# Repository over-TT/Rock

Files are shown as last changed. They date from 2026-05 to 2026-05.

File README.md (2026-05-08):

# Rock

Simple 3D printed RC car with a brushless drone motor. Drive it from your phone over WiFi.

<p align="center">
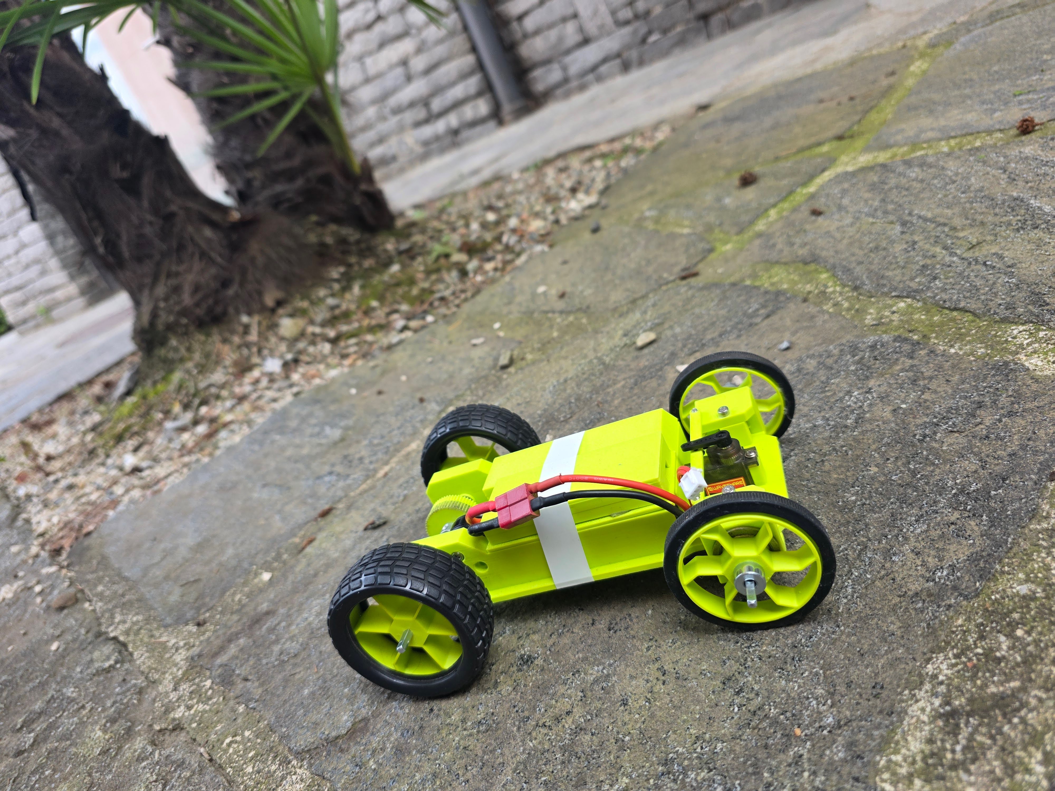
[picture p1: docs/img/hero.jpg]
Rock RC car
  
</p>
---

## Repo

- `firmware/controller/` — controller code
- `firmware/car/` — car code
- `cad/` — 3mf files to print

CAD on MakerWorld: TBD

---

## Parts

**Electronics**
- ReadyToSky MT2204 2300KV brushless drone motor
- EMAX Bullet 20A BLHeli-S ESC
- MG90S servo
- XIAO ESP32-S3 (controller)
- LilyGO T-Energy S3 (car)
- 2S 7.4V 1800mAh LiPo, T-plug ([Reely](https://www.conrad.ch/de/p/reely-modellbau-akkupack-lipo-7-4-v-1800-mah-zellen-zahl-2-racingpack-t-buchse-2901784.html))
- T-plug pigtail
- Wire

**Drivetrain**
- 10T pinion (store bought, fits motor shaft)
- 58T spur gear (printed)
- 1/4" (6.35 mm) square steel drive shaft
- 4x flanged ball bearings (~22 mm OD x ~7.6 mm ID x ~7 mm wide)
- 4x shaft collars for 1/4" square shaft
- Steering linkage

**3D printed parts**
- Body
- 58T spur gear
- 2x front wheels
- 2x rear wheels
- 2x steering knuckles (hold the front wheels, pivot for steering)
- 4x square inserts (adapt the round bearing to the square shaft)
- Battery cover
- ESP cover

**Hardware**
- M3 heat set inserts, screws, nuts
- 4x rubber tires for the printed wheels

---

## Wiring

Car ESP32:

```
ESC signal   -> GPIO 9
Servo signal -> GPIO 10
Servo V+     -> 5V (ESC BEC)
ESP32 5V     -> 5V (ESC BEC)
GND          -> GND
```

GPIO numbers refer to the ESP32 GPIO scheme, not silkscreen pin numbers. If you flash on a different ESP32 variant (XIAO ESP32-S3, ESP32-C3, etc.), check the board's pinout — GPIO 9/10 may map to a different physical pin.

LiPo to ESC via T-plug. Don't run USB and BEC into the ESP32 at the same time.

Controller is the XIAO on USB. No wiring.

---

## Flash

Arduino IDE, `esp32` core 2.0+ from Boards Manager.

Libraries:
- ESP32Servo
- WebSockets (Markus Sattler)

Open `firmware/controller/controller.ino`, pick your board, upload. Same for `firmware/car/car.ino` (LiPo unplugged when uploading).

ESC was set up once with BLHeli Suite using an Arduino Nano running the BLHeli passthrough sketch.

---

## Drive it

1. Power the controller.
2. Phone WiFi → `ROCK_RC`, password `12345678`.
3. Browser → `http://192.168.4.1`
4. Power the car. UI shows "Car: Connected".
5. Left stick throttle, right stick steering. Show Settings for trim, max speed, ramp step.

---

## Tuning

If forward/reverse or left/right is swapped, swap the values in `car.ino`:
- `ESC_FORWARD` / `ESC_REVERSE`
- `SERVO_LEFT` / `SERVO_RIGHT` (90 = center)

Trim, max speed, and ramp step are sliders in the UI.

---

## TODO

- CAD on MakerWorld
- Wiring diagram image
- Demo video
- Battery voltage in UI
- Proper retention for battery / ESC / ESP32 (snap-fit or clamps instead of tape)

---

## License

- Code (`firmware/`): MIT — see [LICENSE](LICENSE)
- CAD (`cad/`): CC BY-SA 4.0 — see [cad/LICENSE](cad/LICENSE)

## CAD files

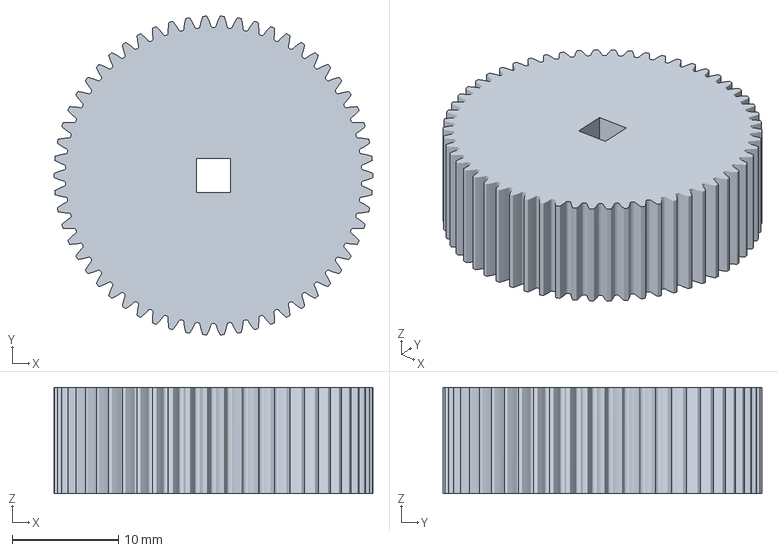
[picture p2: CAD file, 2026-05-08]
cad/spur_58t.3mf
30.0 x 30.0 x 10.0 mm

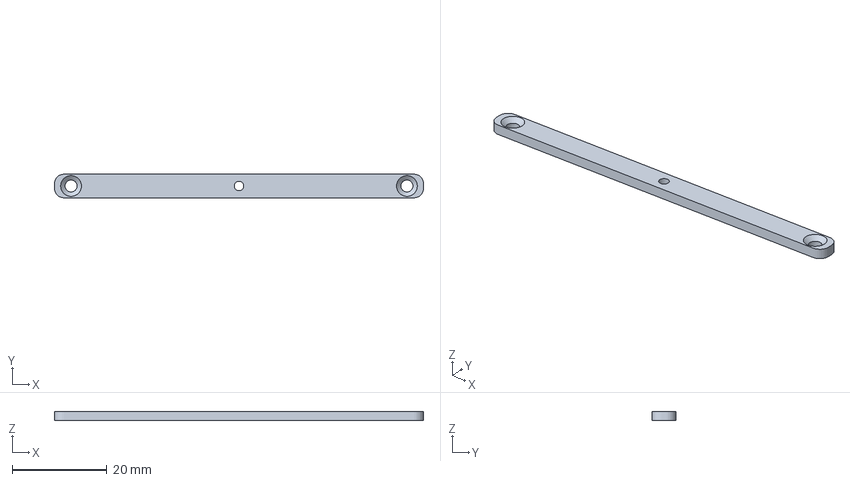
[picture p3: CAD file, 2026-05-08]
cad/steering_link.3mf
78.0 x 5.00 x 2.00 mm

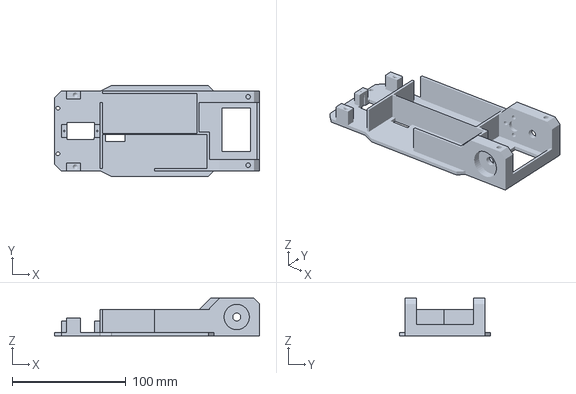
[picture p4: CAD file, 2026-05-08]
cad/chassis.3mf
180.0 x 80.0 x 33.0 mm

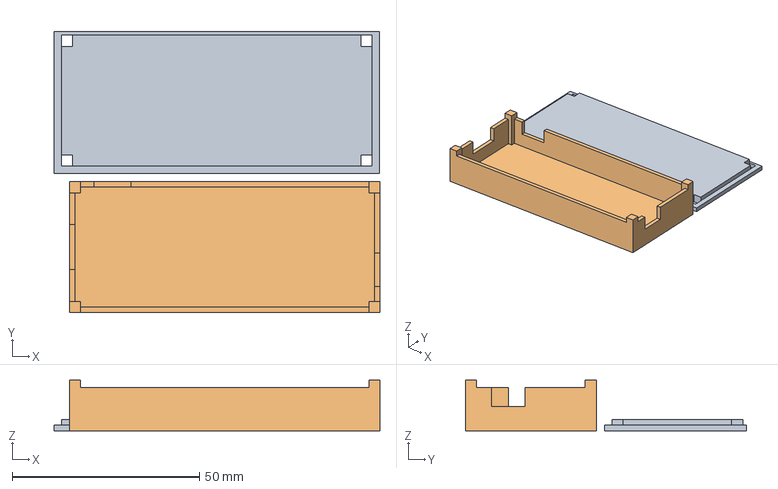
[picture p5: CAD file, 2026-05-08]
cad/battery_cover.3mf
87.1 x 75.1 x 13.5 mm

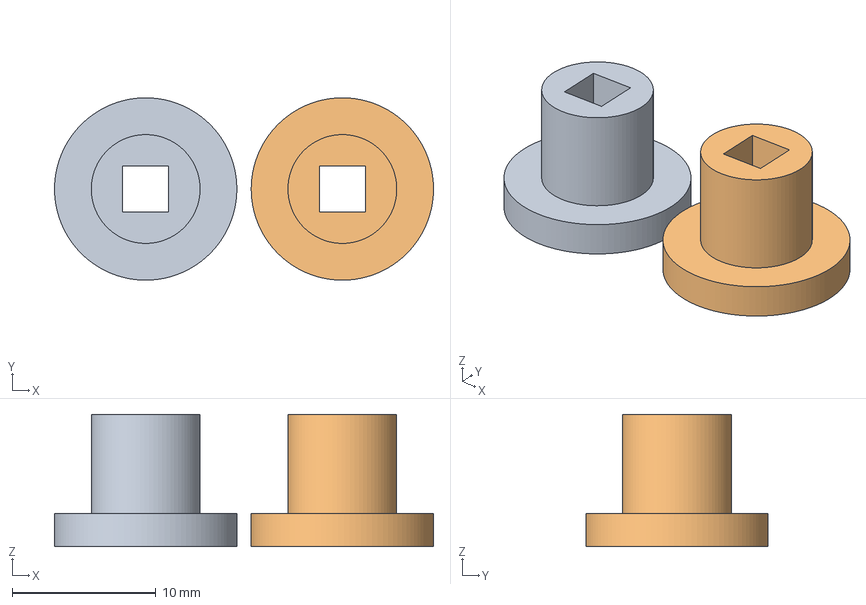
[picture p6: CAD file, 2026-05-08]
cad/bearing_insert.3mf
26.4 x 12.7 x 9.20 mm

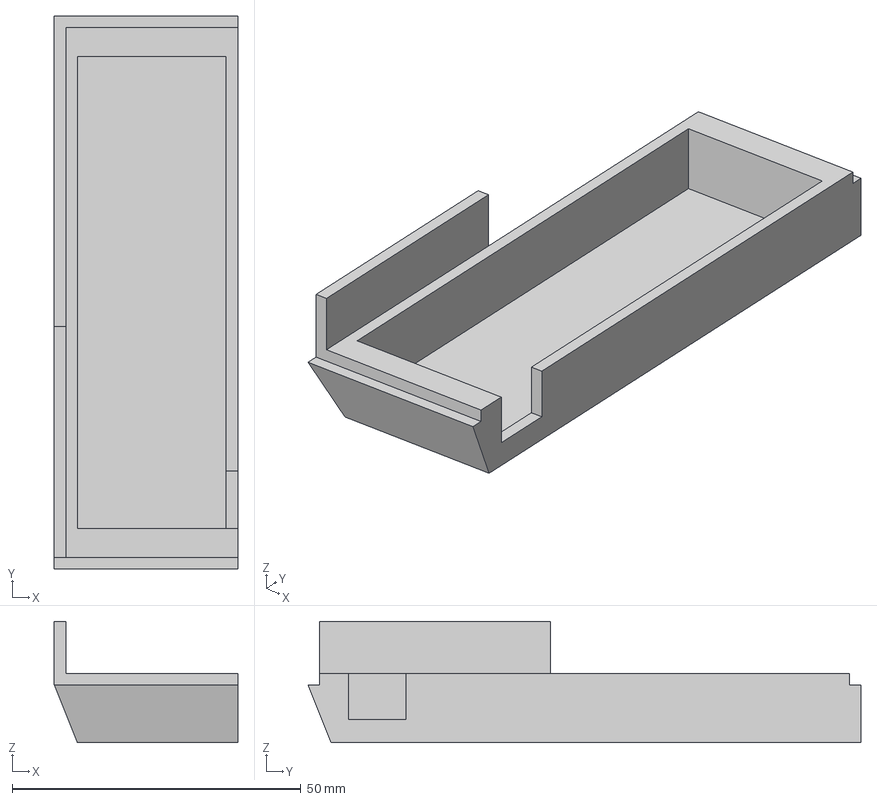
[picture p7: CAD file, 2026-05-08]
cad/electronics_cover.3mf
31.8 x 95.8 x 21.0 mm

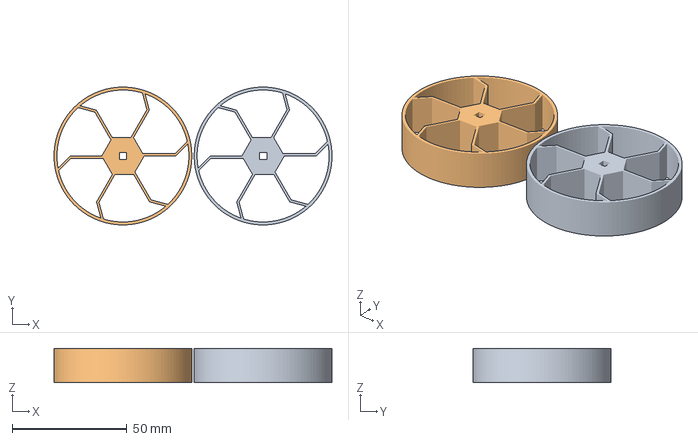
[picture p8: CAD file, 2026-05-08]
cad/rear_wheel.3mf
121.0 x 60.0 x 15.0 mm

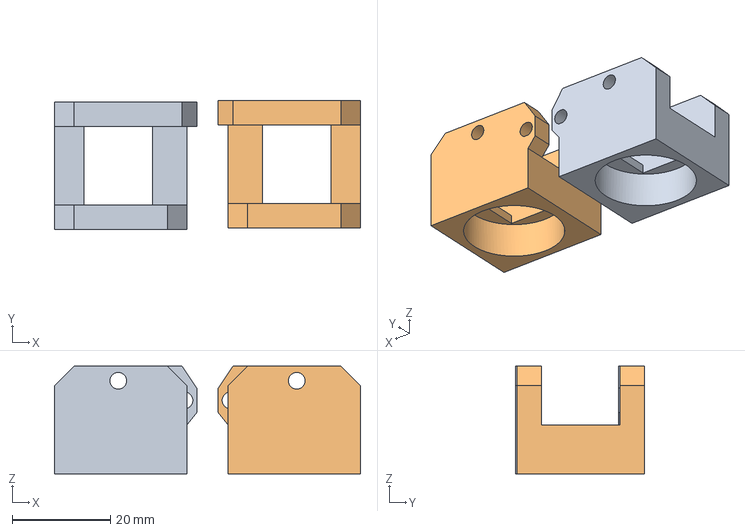
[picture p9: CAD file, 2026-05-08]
cad/steering_knuckle .3mf
62.4 x 26.3 x 22.0 mm

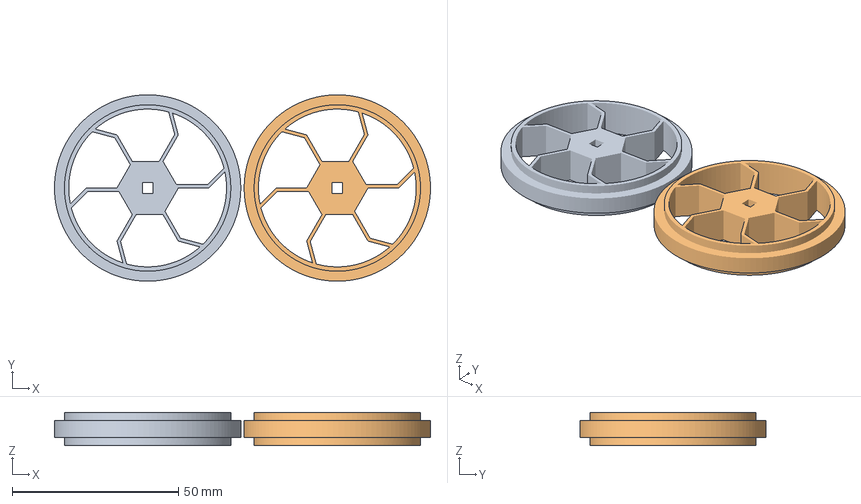
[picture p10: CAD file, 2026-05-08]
cad/front_wheel.3mf
113.0 x 56.0 x 10.0 mm

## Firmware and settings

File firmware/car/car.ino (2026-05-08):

// ROCK RC - Car firmware (ESP32)
// Receives ESP-NOW control packets, drives the ESC and steering servo,
// and reports status back to the controller. Failsafe stops the car if
// packets stop arriving.
// Licensed under the MIT License. See LICENSE at the repository root.

#include <WiFi.h>
#include <esp_now.h>
#include <esp_wifi.h>
#include <esp_arduino_version.h>
#include <ESP32Servo.h>

Servo esc;
Servo steeringServo;

// ===== PINS =====
// These pins are for the board used in this build.
// Change them if using a different ESP32 board.
// Always check the actual GPIO pinout before wiring.
const int ESC_PIN = 9;
const int SERVO_PIN = 10;

// ===== ESP-NOW SETTINGS =====
const int WIFI_CHANNEL = 6;

// ===== ESP-NOW TYPES =====
const uint8_t TYPE_CONTROL = 1;
const uint8_t TYPE_STATUS  = 2;

// ===== ESC SETTINGS =====
const int ESC_MIN_ATTACH = 1000;
const int ESC_MAX_ATTACH = 2000;

const int ESC_FORWARD = 1200;
const int ESC_NEUTRAL = 1500;
const int ESC_REVERSE = 1700;

// If motor direction is backwards, swap ESC_FORWARD and ESC_REVERSE.

// ===== SERVO SETTINGS =====
const int SERVO_MIN_ATTACH = 500;
const int SERVO_MAX_ATTACH = 2500;

const int SERVO_LEFT = 120;
const int SERVO_CENTER = 90;
const int SERVO_RIGHT = 60;

// ===== SAFETY =====
unsigned long lastCommandTime = 0;
const unsigned long FAILSAFE_TIME = 500;

// ===== MOTOR RAMPING =====
const unsigned long RAMP_INTERVAL = 20;
unsigned long lastRampTime = 0;

// ===== STATUS SENDING =====
const unsigned long STATUS_INTERVAL = 200;
unsigned long lastStatusSend = 0;

// Control values
int targetMotor = 0;
int currentMotor = 0;
int targetSteer = 0;

int servoOffset = 0;
int maxSpeed = 60;
int rampStep = 4;

int currentThrottlePulse = ESC_NEUTRAL;
int currentSteeringAngle = SERVO_CENTER;

bool failsafeActive = false;

uint8_t controllerMac[6];
bool controllerKnown = false;
bool controllerPeerAdded = false;
bool needAddControllerPeer = false;

uint32_t lastSeqReceived = 0;

// ===== CONTROL PACKET =====
// Must match controller code EXACTLY
typedef struct __attribute__((packed)) {
  uint8_t type;
  int16_t motor;
  int16_t steer;
  int16_t servoOffset;
  uint8_t maxSpeed;
  uint8_t rampStep;
  uint32_t seq;
} ControlPacket;

// ===== STATUS PACKET =====
// Must match controller code EXACTLY
typedef struct __attribute__((packed)) {
  uint8_t type;
  uint32_t lastSeqReceived;
  int16_t targetMotor;
  int16_t currentMotor;
  int16_t steeringAngle;
  uint8_t maxSpeed;
  uint8_t rampStep;
  uint8_t failsafeActive;
} CarStatusPacket;

ControlPacket incoming;
CarStatusPacket statusPacket;

void printMac(const uint8_t *mac) {
  for (int i = 0; i < 6; i++) {
    if (mac[i] < 16) Serial.print("0");
    Serial.print(mac[i], HEX);
    if (i < 5) Serial.print(":");
  }
}

void addControllerPeerIfNeeded() {
  if (!controllerKnown) return;
  if (!needAddControllerPeer && controllerPeerAdded) return;

  if (esp_now_is_peer_exist(controllerMac)) {
    controllerPeerAdded = true;
    needAddControllerPeer = false;
    return;
  }

  esp_now_peer_info_t peerInfo = {};
  memcpy(peerInfo.peer_addr, controllerMac, 6);
  peerInfo.channel = WIFI_CHANNEL;
  peerInfo.encrypt = false;

  if (esp_now_add_peer(&peerInfo) == ESP_OK) {
    controllerPeerAdded = true;
    needAddControllerPeer = false;

    Serial.print("Controller paired: ");
    printMac(controllerMac);
    Serial.println();
  } else {
    Serial.println("Failed to add controller peer");
  }
}

void sendStatusToController() {
  if (!controllerPeerAdded) return;

  statusPacket.type = TYPE_STATUS;
  statusPacket.lastSeqReceived = lastSeqReceived;
  statusPacket.targetMotor = targetMotor;
  statusPacket.currentMotor = currentMotor;
  statusPacket.steeringAngle = currentSteeringAngle;
  statusPacket.maxSpeed = maxSpeed;
  statusPacket.rampStep = rampStep;
  statusPacket.failsafeActive = failsafeActive ? 1 : 0;

  esp_now_send(controllerMac, (uint8_t*)&statusPacket, sizeof(statusPacket));
}

void applyMotorPulseFromValue(int motorValue) {
  motorValue = constrain(motorValue, -100, 100);

  int pulse;

  if (abs(motorValue) < 5) {
    pulse = ESC_NEUTRAL;
  } else if (motorValue > 0) {
    pulse = map(motorValue, 0, 100, ESC_NEUTRAL, ESC_FORWARD);
  } else {
    pulse = map(motorValue, 0, -100, ESC_NEUTRAL, ESC_REVERSE);
  }

  pulse = constrain(pulse, ESC_MIN_ATTACH, ESC_MAX_ATTACH);

  currentThrottlePulse = pulse;
  esc.writeMicroseconds(currentThrottlePulse);
}

void applySteering(int steerValue) {
  steerValue = constrain(steerValue, -100, 100);

  int angle;

  if (abs(steerValue) < 5) {
    angle = SERVO_CENTER;
  } else {
    angle = map(steerValue, -100, 100, SERVO_LEFT, SERVO_RIGHT);
  }

  angle += servoOffset;
  angle = constrain(angle, 0, 180);

  currentSteeringAngle = angle;
  steeringServo.write(currentSteeringAngle);
}

void updateMotorRamp() {
  if (millis() - lastRampTime < RAMP_INTERVAL) return;
  lastRampTime = millis();

  int difference = targetMotor - currentMotor;

  if (difference == 0) {
    applyMotorPulseFromValue(currentMotor);
    return;
  }

  int step = rampStep;

  // Symmetric ramping:
  // forward, reverse, speeding up, slowing down all use same step.
  if (abs(difference) <= step) {
    currentMotor = targetMotor;
  } else {
    if (difference > 0) {
      currentMotor += step;
    } else {
      currentMotor -= step;
    }
  }

  applyMotorPulseFromValue(currentMotor);
}

void stopCarHard() {
  targetMotor = 0;
  currentMotor = 0;
  targetSteer = 0;

  currentThrottlePulse = ESC_NEUTRAL;
  currentSteeringAngle = SERVO_CENTER + servoOffset;
  currentSteeringAngle = constrain(currentSteeringAngle, 0, 180);

  esc.writeMicroseconds(currentThrottlePulse);
  steeringServo.write(currentSteeringAngle);
}

void handleEspNowReceive(const uint8_t *srcMac, const uint8_t *data, int len) {
  if (len != sizeof(ControlPacket)) return;

  ControlPacket temp;
  memcpy(&temp, data, sizeof(temp));

  if (temp.type != TYPE_CONTROL) return;

  memcpy(&incoming, &temp, sizeof(incoming));

  memcpy(controllerMac, srcMac, 6);
  controllerKnown = true;
  needAddControllerPeer = true;

  int receivedMotor = constrain(incoming.motor, -100, 100);
  int receivedSteer = constrain(incoming.steer, -100, 100);

  servoOffset = constrain(incoming.servoOffset, -30, 30);
  maxSpeed = constrain(incoming.maxSpeed, 10, 100);
  rampStep = constrain(incoming.rampStep, 1, 25);

  targetMotor = (receivedMotor * maxSpeed) / 100;

  if (abs(receivedMotor) < 5) {
    targetMotor = 0;
  }

  targetSteer = receivedSteer;
  lastSeqReceived = incoming.seq;

  applySteering(targetSteer);

  lastCommandTime = millis();
  failsafeActive = false;
}

#if ESP_ARDUINO_VERSION_MAJOR >= 3
void onDataRecv(const esp_now_recv_info_t *info, const uint8_t *data, int len) {
  handleEspNowReceive(info->src_addr, data, len);
}
#else
void onDataRecv(const uint8_t *mac, const uint8_t *data, int len) {
  handleEspNowReceive(mac, data, len);
}
#endif

void setup() {
  Serial.begin(115200);

  // ===== START SAFE =====
  esc.setPeriodHertz(50);
  esc.attach(ESC_PIN, ESC_MIN_ATTACH, ESC_MAX_ATTACH);
  esc.writeMicroseconds(ESC_NEUTRAL);

  steeringServo.setPeriodHertz(50);
  steeringServo.attach(SERVO_PIN, SERVO_MIN_ATTACH, SERVO_MAX_ATTACH);
  steeringServo.write(SERVO_CENTER);

  Serial.println("Starting ESC at neutral 1500 us...");
  Serial.println("Waiting 5 seconds for ESC to arm...");
  delay(5000);

  // ===== ESP-NOW SETUP =====
  WiFi.mode(WIFI_STA);
  esp_wifi_set_channel(WIFI_CHANNEL, WIFI_SECOND_CHAN_NONE);

  Serial.println();
  Serial.println("RC Car ESP-NOW Receiver");
  Serial.print("Car MAC address: ");
  Serial.println(WiFi.macAddress());
  Serial.print("ESP-NOW channel: ");
  Serial.println(WIFI_CHANNEL);

  if (esp_now_init() != ESP_OK) {
    Serial.println("ESP-NOW init failed");
    return;
  }

  esp_now_register_recv_cb(onDataRecv);

  lastCommandTime = millis();
  lastRampTime = millis();
  lastStatusSend = millis();

  Serial.println("Receiver ready.");
}

void loop() {
  addControllerPeerIfNeeded();

  if (millis() - lastCommandTime > FAILSAFE_TIME) {
    if (!failsafeActive) {
      stopCarHard();
      failsafeActive = true;
    }
  } else {
    updateMotorRamp();
  }

  if (millis() - lastStatusSend > STATUS_INTERVAL) {
    lastStatusSend = millis();
    sendStatusToController();
  }
}

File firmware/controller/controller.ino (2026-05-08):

// ROCK RC - Controller firmware (ESP32 / Seeed XIAO ESP32-S3)
// Hosts the phone web UI and bridges joystick input to the car over ESP-NOW.
// Licensed under the MIT License. See LICENSE at the repository root.

#include <WiFi.h>
#include <WebServer.h>
#include <WebSocketsServer.h>
#include <esp_now.h>
#include <esp_wifi.h>
#include <esp_arduino_version.h>

// ===== WIFI / ESP-NOW SETTINGS =====
const char* ssid = "ROCK_RC";
const char* password = "12345678";

const int WIFI_CHANNEL = 6;

WebServer server(80);
WebSocketsServer webSocket = WebSocketsServer(81);

// ===== ESP-NOW TYPES =====
const uint8_t TYPE_CONTROL = 1;
const uint8_t TYPE_STATUS  = 2;

uint8_t broadcastAddress[] = {0xFF, 0xFF, 0xFF, 0xFF, 0xFF, 0xFF};

uint8_t carMac[6];
bool carKnown = false;
bool carPeerAdded = false;
bool needAddCarPeer = false;

// ===== CONTROL PACKET =====
// Must match RC car code EXACTLY
typedef struct __attribute__((packed)) {
  uint8_t type;
  int16_t motor;        // -100 to 100
  int16_t steer;        // -100 to 100
  int16_t servoOffset;  // -30 to +30 degrees
  uint8_t maxSpeed;     // 10 to 100 percent
  uint8_t rampStep;     // 1 to 25
  uint32_t seq;
} ControlPacket;

// ===== STATUS PACKET =====
// Must match RC car code EXACTLY
typedef struct __attribute__((packed)) {
  uint8_t type;
  uint32_t lastSeqReceived;
  int16_t targetMotor;
  int16_t currentMotor;
  int16_t steeringAngle;
  uint8_t maxSpeed;
  uint8_t rampStep;
  uint8_t failsafeActive;
} CarStatusPacket;

ControlPacket controlPacket;
CarStatusPacket carStatus;

uint32_t seqNum = 0;

// Latest values from phone
int currentMotor = 0;
int currentSteer = 0;
int currentServoOffset = 0;
int currentMaxSpeed = 60;
int currentRampStep = 4;

unsigned long lastPhoneCommand = 0;
const unsigned long PHONE_TIMEOUT = 500;

unsigned long lastCarStatusTime = 0;
unsigned long lastStatusWebSend = 0;
const unsigned long WEB_STATUS_INTERVAL = 200;

// ===== HTML PAGE =====
const char htmlPage[] PROGMEM = R"rawliteral(
<!DOCTYPE html>
<html>
<head>
  <meta name="viewport" content="width=device-width, initial-scale=1.0, user-scalable=no">
  <title>ROCK RC Controller</title>

  <style>
    body {
      margin: 0;
      font-family: Arial, sans-serif;
      background: #111;
      color: white;
      text-align: center;
      overflow: hidden;
    }

    h2 {
      margin: 10px 0 4px 0;
      font-size: 23px;
    }

    .topBar {
      display: flex;
      justify-content: center;
      align-items: center;
      gap: 8px;
      flex-wrap: wrap;
      padding: 3px 8px;
    }

    .toggleBtn {
      background: #2a2a2a;
      color: white;
      border: 1px solid #555;
      border-radius: 10px;
      padding: 7px 12px;
      font-size: 14px;
    }

    .statusRow {
      display: flex;
      justify-content: center;
      gap: 8px;
      flex-wrap: wrap;
      padding: 3px 8px;
    }

    .statusBox {
      background: #1b1b1b;
      border: 1px solid #333;
      border-radius: 10px;
      padding: 6px 9px;
      min-width: 120px;
      font-size: 12px;
    }

    .good { color: #55ff88; }
    .bad { color: #ff6666; }
    .warn { color: #ffcc66; }

    .settings {
      display: flex;
      justify-content: center;
      gap: 10px;
      flex-wrap: wrap;
      padding: 5px 10px;
      font-size: 13px;
      max-height: 140px;
      overflow: hidden;
      transition: max-height 0.2s ease, opacity 0.2s ease, padding 0.2s ease;
      opacity: 1;
    }

    .settings.collapsed {
      max-height: 0;
      opacity: 0;
      padding-top: 0;
      padding-bottom: 0;
      pointer-events: none;
    }

    .settingBox {
      background: #1b1b1b;
      border: 1px solid #333;
      border-radius: 10px;
      padding: 7px;
      min-width: 155px;
    }

    input[type="range"] {
      width: 140px;
    }

    .container {
      display: flex;
      justify-content: space-around;
      align-items: center;
      height: calc(100vh - 165px);
      gap: 18px;
      padding: 8px;
    }

    .stickBox {
      display: flex;
      flex-direction: column;
      align-items: center;
    }

    .label {
      font-size: 19px;
      margin-bottom: 9px;
    }

    .joystick {
      width: 220px;
      height: 220px;
      background: #222;
      border: 3px solid #555;
      border-radius: 50%;
      position: relative;
      touch-action: none;
    }

    .knob {
      width: 80px;
      height: 80px;
      background: #ddd;
      border-radius: 50%;
      position: absolute;
      left: 70px;
      top: 70px;
      box-shadow: 0 0 15px #000;
    }

    .value {
      margin-top: 9px;
      font-size: 15px;
      color: #bbb;
    }

    @media (max-height: 600px) {
      h2 { display: none; }

      .statusBox {
        font-size: 11px;
        padding: 4px 7px;
        min-width: 105px;
      }

      .container {
        height: calc(100vh - 95px);
      }

      .joystick {
        width: 190px;
        height: 190px;
      }

      .knob {
        width: 70px;
        height: 70px;
        left: 60px;
        top: 60px;
      }
    }
  </style>
</head>

<body>
  <h2>ROCK RC Car Control</h2>

  <div class="topBar">
    <button id="settingsToggle" class="toggleBtn">Show Settings</button>
  </div>

  <div class="statusRow">
    <div class="statusBox">
      Phone: <span id="phoneStatus" class="bad">Disconnected</span>
    </div>
    <div class="statusBox">
      Car: <span id="carStatus" class="bad">Searching</span>
    </div>
    <div class="statusBox">
      Last seen: <span id="lastSeen">---</span>
    </div>
    <div class="statusBox">
      Seq: <span id="seqVal">---</span>
    </div>
    <div class="statusBox">
      Motor: <span id="motorStatus">---</span>
    </div>
    <div class="statusBox">
      Servo: <span id="servoStatus">---</span>
    </div>
  </div>

  <div id="settingsPanel" class="settings collapsed">
    <div class="settingBox">
      <div>Servo offset: <span id="offsetVal">0</span>°</div>
      <input id="offsetSlider" type="range" min="-30" max="30" value="0">
    </div>

    <div class="settingBox">
      <div>Max speed: <span id="speedVal">60</span>%</div>
      <input id="speedSlider" type="range" min="10" max="100" value="60">
    </div>

    <div class="settingBox">
      <div>Ramp step: <span id="rampVal">4</span></div>
      <input id="rampSlider" type="range" min="1" max="25" value="4">
    </div>
  </div>

  <div class="container">
    <div class="stickBox">
      <div class="label">Motor</div>
      <div id="motorJoy" class="joystick">
        <div id="motorKnob" class="knob"></div>
      </div>
      <div id="motorVal" class="value">Motor: 0</div>
    </div>

    <div class="stickBox">
      <div class="label">Steering</div>
      <div id="steerJoy" class="joystick">
        <div id="steerKnob" class="knob"></div>
      </div>
      <div id="steerVal" class="value">Steer: 0</div>
    </div>
  </div>

<script>
let motor = 0;
let steer = 0;

let servoOffset = 0;
let maxSpeed = 60;
let rampStep = 4;

let ws;
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
